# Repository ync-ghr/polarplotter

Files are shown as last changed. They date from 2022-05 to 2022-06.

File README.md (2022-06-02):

# Polar Plotter
Ein Projekt der Hochschule Pforzheim.

(https://youtu.be/9DOyNeQ_HOg)

- [Benötigte Komponenten](#benötigte-komponenten)<br>
  - [Zukaufteile](#zukaufteile)<br>
  - [3D-Druck Teile](#3d-druck-teile)<br>
- [Installation Polargraph Software](#installation-polargraph-software)<br>
- [Aufbau des Plotters](#aufbau-des-plotters)<br>
- [Einstellungen in der Software](#einstellungen-in-der-software)<br>

## Benötigte Komponenten

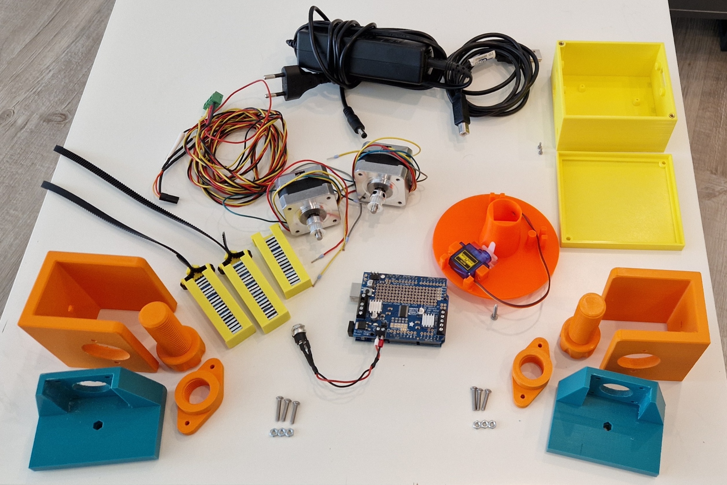
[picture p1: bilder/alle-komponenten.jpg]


### Zukaufteile

- Arduino Uno: http://store.arduino.cc/products/arduino-uno-rev3

- Adafruit Motor Shiled v2: https://www.adafruit.com/product/1438

- Servomotor: https://www.amazon.de/dp/B07CYZK379?ref_=cm_sw_r_cp_ud_dp_AW2FQ5ZJ4909N2ZZ1QXP
  - 5 V
  - 22,2 x 11,8 x 31 mm

- Schrittmotoren: https://www.adafruit.com/product/324#technical-details
  - 200 steps per revolution
  - 1.8 degrees
  - 12 V
  - 350 mA

- Zahnriemen und Zahnräder aus 3D-Drucker Bereich: https://www.amazon.de/dp/B07QH94G71?ref_=cm_sw_r_cp_ud_dp_NBP2886NY2H1YNJAXYJZ
  - GT2 2 mm
  - Rastermaß 6 mm
  - 5 m Länge

- Gewichte: https://www.amazon.de/dp/B08F2H4TB8?ref_=cm_sw_r_cp_ud_dp_EE6H5DKYBR2R5X1NX4WT 
  - 100 g + 2 x 60 g

- 12 V Netzteil

- Schrauben und Muttern:
  - 3x Rutex Gewindebuchse M3x5.7: https://www.ruthex.de/products/ruthex-gewindeeinsatz-m3-100-stuck-rx-m3x5-7-messing-gewindebuchsen
  - 8x M3x10 Schraube
  - 4x M3x15 Schraube
  - 3x M3x18 Schraube
  - 1x M3x30 Schraube
  - 6x M3 Mutter
  - 6x M2x5 Schraube (spitz)

### 3D-Druck Teile

STL-Dateien aus `/bauteile` auf dem 3D-Drucker herstellen. Die Komponenten und deren Funktionsweise werden [hier](stl\README.md) erläutert.

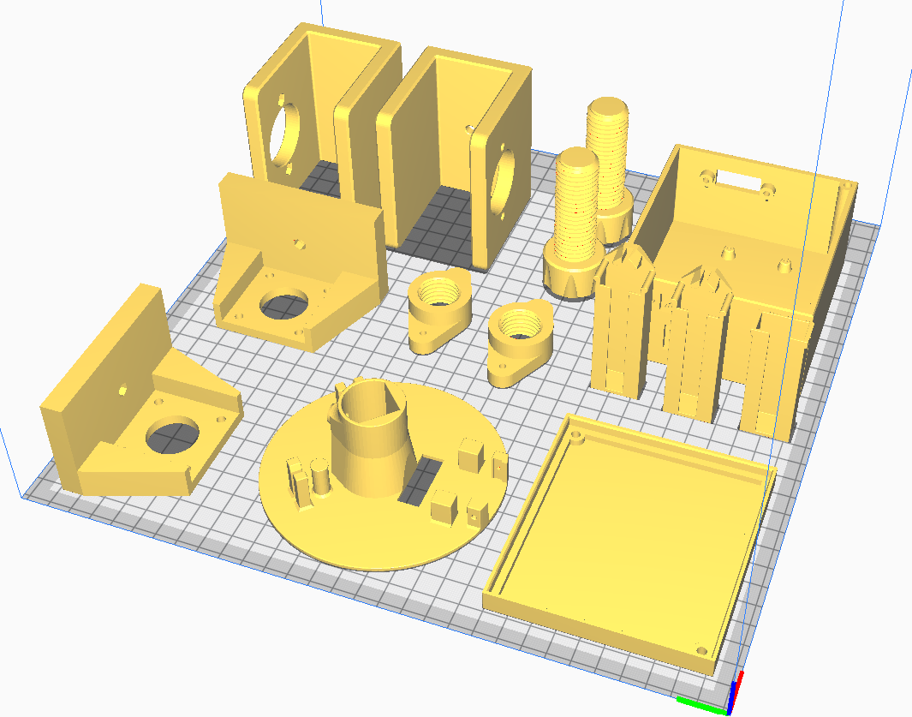
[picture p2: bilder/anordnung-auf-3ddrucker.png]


## Installation Polargraph Software

- Herunterladen und installieren von Arduino IDE v1.8.5: https://www.arduino.cc/en/software/OldSoftwareReleases#previous

- Herunterladen des Polargraphcontollers: https://github.com/euphy/polargraphcontroller/releases/tag/2017-11-01-20-30

- Dieses Verzeichnis (polargraph.2017-11-01.zip) entpacken und öffnen. Darin ist ein Ordner `\arduino-source\polargraph-server-a1` enthalten. Diesen in den Arduino Ordner verschieben (`C:\Users\"PCNAME"\Documents\Arduino`).

- Den Inhalt des Ordners `\arduino-source\libraries` in den Ordner `C:\Users\"PCNAME"\Documents\Arduino\libraries` verschieben. 
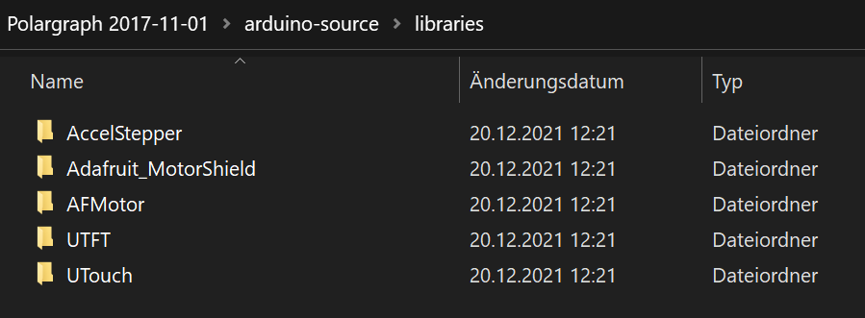
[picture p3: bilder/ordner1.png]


- Anschließend Arduino IDE starten und Arduino über USB mit dem PC verbinden.

- `File -> Sketchbook -> polargraph_server_a1` auswählen und im Tab polargraph_server_a1 unter 1. den Controller auf MC_UNO einstellen. Unter 3. die verwendeten Motortreiber auswählen.

  ```
  // 1. 
  //Uncomment the line for the kind of board you have.
  #ifndef MICROCONTROLLER
  #define MICROCONTROLLER MC_UNO
  //#define MICROCONTROLLER MC_MEGA
  #endif

  // 3. 
  //Specify what kind of motor driver you are using
  #define ADAFRUIT_MOTORSHIELD_V2
  #include <Wire.h>
  #include <Adafruit_MotorShield.h>
  #include "utility/Adafruit_PWMServoDriver.h"
  ```

- Auswahl des Boards: `Tools -> Board -> Arduino Uno`

- Setzen des angeschlossenen Ports: `Tools -> Port -> COMx`

- Auf den Pfeil klicken, um den Code auf den Arduino zu laden. Warten, bis Hochladen abgeschlossen ist.

- Herunterladen und installieren von Processing v2.2.1: https://processing.org/download?processing

- Processing starten und wieder schließen.

- Im bereits heruntergeladenen Verzeichnis (polargraph.2017-11-01) den Inhalt des Ordners `Polargraph.2017-11-01\processing-source\Processing libraries` nach `C:\Users\"PCNAME"\Documents\Processing\libraries` kopieren.
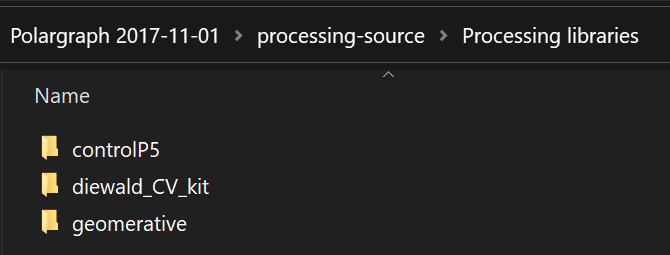
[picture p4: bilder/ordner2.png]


- Anschließend den gesamten Ordner `Polargraph 2017-11-01\processing-source\polargraphcontroller` in den Processing Sketchbook Ordner (`C:\Users\"PCNAME"\Documents\Processing`) kopieren.

- Processing erneut starten und `File -> Sketchbook -> polargraphcontroller` öffnen.

- Run drücken, um den Controller zu starten.

## Aufbau des Plotters

- Zusammenbau der beiden Motorhalterungen aus den 3D-Druckteilen, jeweils 3 Schrauben (2st M3x15, 1st M3x18) und 3 Muttern.

 
- Festschrauben der Motoren an der Halterung, Befestigung am Zeichenbrett und Anbringung der Zahnräder.
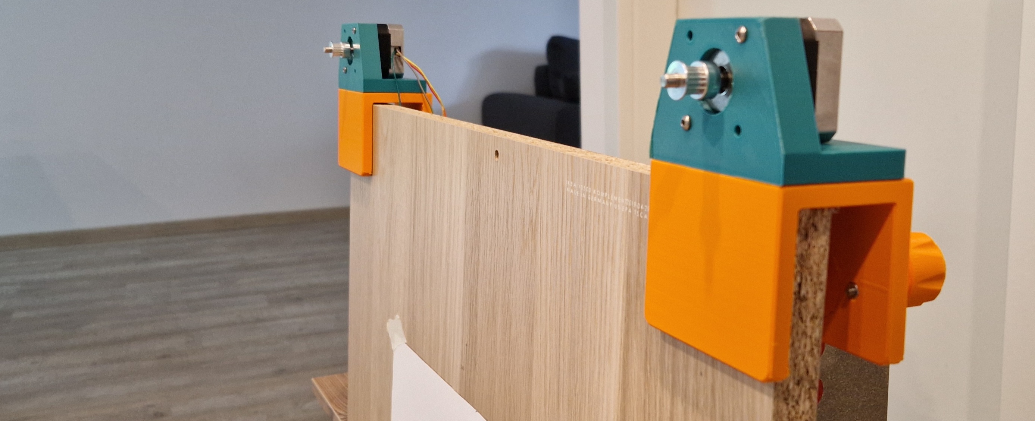
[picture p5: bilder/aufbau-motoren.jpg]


- Anbringen des Motorshields auf dem Arduino und löten der Pins. Anschließend vorbereiten der 12 V Stromversorgung.
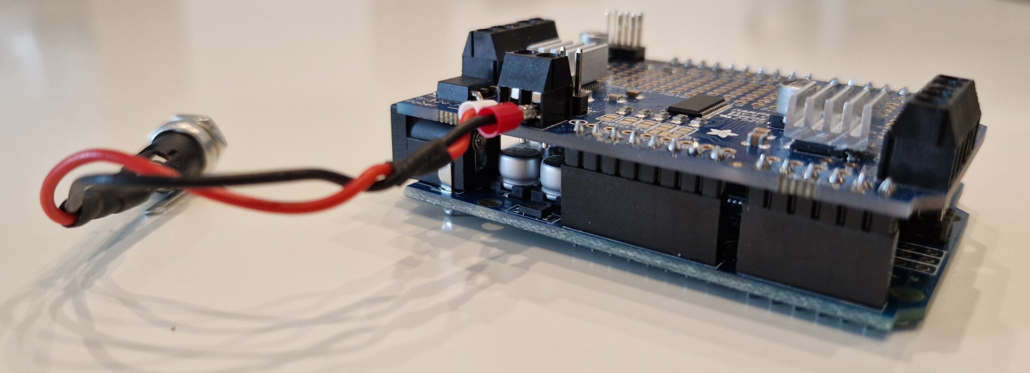
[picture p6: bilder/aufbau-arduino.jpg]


- Einlegen der Gewichte in die Halterungen und Befestigung des Gummiriemens durch Verkanten der Zähne. Riemen soll einmal gespiegelt angebracht werden (siehe Bild).
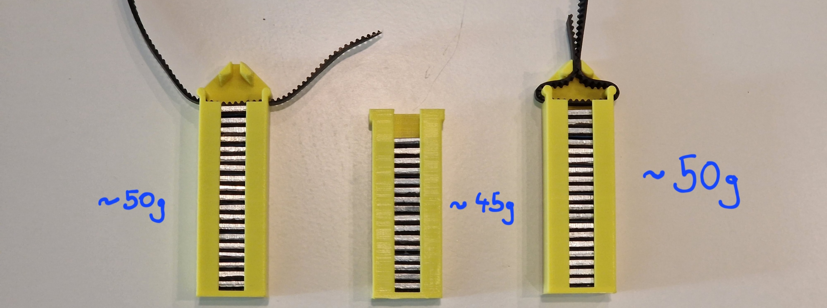
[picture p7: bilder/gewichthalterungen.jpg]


- Anbringen des Servomotors und der Gewichthalterung an der Gondel. Befestigung des Gummiriemens durch Verkanten. Verlängerungskabel für den Servomotor verbinden. Einschmelzen des Gewindes in die Bohrung.
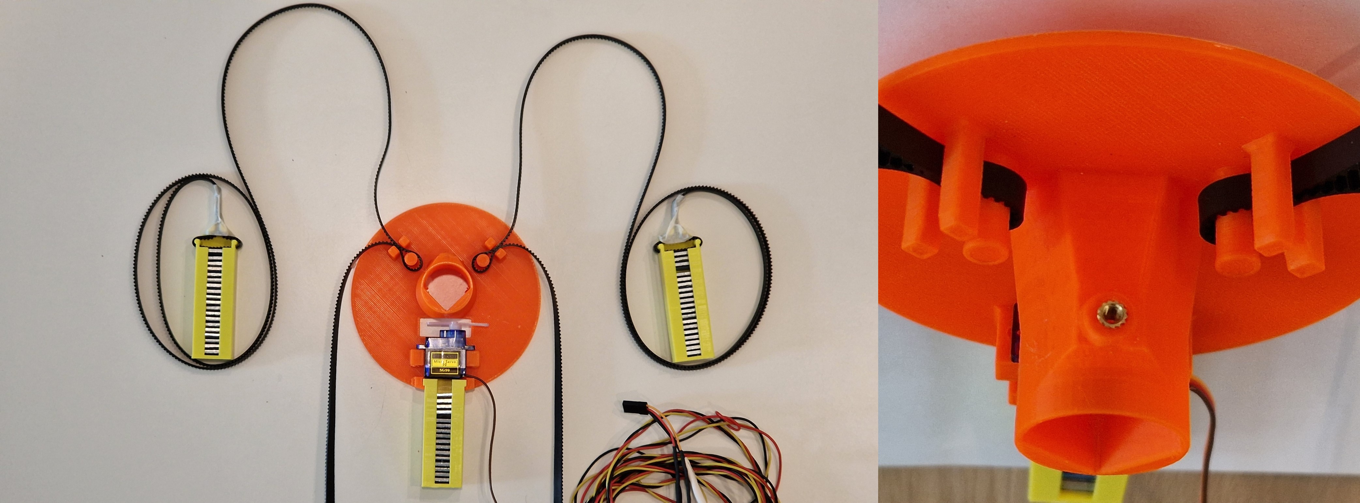
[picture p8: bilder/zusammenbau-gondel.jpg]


- Aufsetzen der Konstruktion über die Zahnräder und Kabel auf die Rückseite führen.
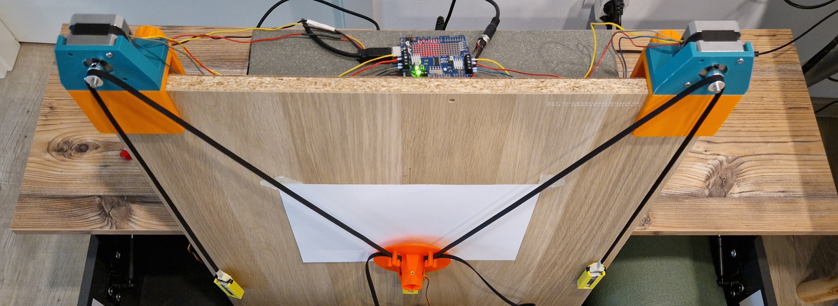
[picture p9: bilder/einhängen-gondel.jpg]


- Verkabelung der beiden Schrittmotoren an die Klemmen (Blau/Grün ein Coil, Gelb/Rot ein Coil) und aufstecken des Servosteckers an die Servo 2 Pins. Herstellen der 12 V Stromversorgung und der USB-Verbindung mit einem Windows-PC.


- Anbringung eines Zeichenblattes auf dem Zeichenbrett.

- Zum Schluss kann der Arduino in das gedruckte Gehäuse gesetzt und verschraubt werden.

## Einstellungen in der Software

### SETUP

Einstellungen für die Abmessungen des Zeichenbretts und des Zeichenblatts sowie weitere grundsätzliche Einstellungen. Im Tab SETUP.

| Feldname | Wert | Bedeutung |
|---|----:|---|
| MM PER REV | 64 | Drehung des Riemens pro Schritt |
| STEPS PER REV | 1090 | Schritte pro Umdrehung (alt. 400) |
| STEP MULTIPLIER | 6 | Skalierung der Schritte (alt. 16)|
| MASCHINE WIDTH | - | Breite des Zeichenbretts (Distanz zwischen Innenseite der Zahnräder) |
| MASCHINE HIGHT | - | Höhe des Zeichenbretts |
| PAGE WIDTH | - | Breite des Zeichenblatts |
| PAGE HIGHT | - | Höhe des Zeichenblatts |
| PAGE POS X | - | X-Position des Blatts |
| PAGE POS Y | - | Y-Position des Blatts |
| HOME POS X | - | X-Position des Homepunkts |
| HOME POS Y | - | Y-Position des Homepunkts |
| PEN UP POSTION | - | Winkel des Servos für angehobenen Stift |
| PEN DOWN POSITION | - | Winkel des Servos für abgesetzten Stift |
| MOTOR MAX SPEED | 1000 | Maximalgeschwindigkeit des Motors |
| MOTOR MAX ACCELERATION | 400 | Maximalbeschleunigung des Motors |

- Außerdem muss der `SERIAL PORT...` eingestellt werden. Ist die Verbindung erfolgreich, erscheint in grün `Polargraph READY! (Uno)`

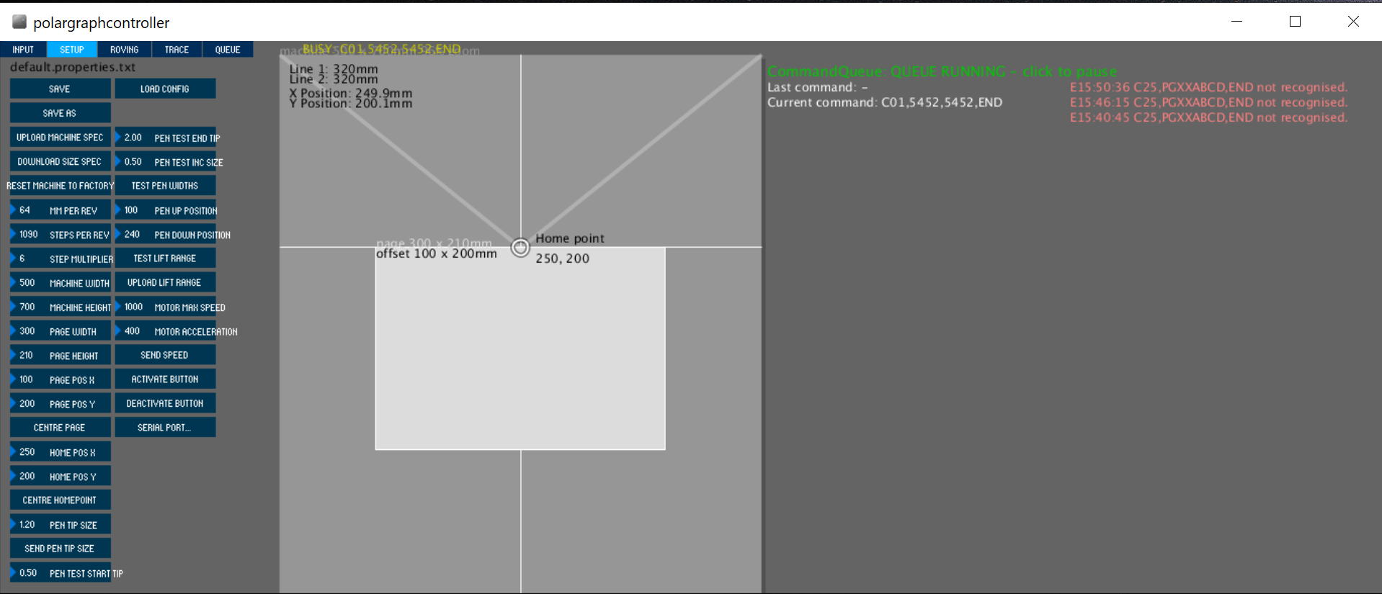
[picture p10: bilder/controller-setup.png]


### INPUT

Einstellungen, die das Zeichenobjekt betreffen. Über Tab INPUT.

- Zuerst muss die Gondel manuell so eingehängt werden, dass sich der Stift direkt über dem Homepunkt befindet. Anschließend kann über den Button `SET HOME` dieser Punkt abgespeichert werden.

- Durch Klicken auf den Button `LOAD IMAGE FILE` kann eine Bilddatei ausgewählt und auf dem Brett positioniert werden. Über `RESIZE IMAGE` und `MOVE IMAGE` kann die Größe und Position noch verändert werden.

- Es gibt die Möglichkeit ein Bild schattiert zu zeichnen, dafür `INPUT -> RENDER PIXELS`. Alternativ kann die Kontur eines Vektors oder Bilds gezeichnet werden, dafür `TRACE -> CAPUTER`, anschließend `DRAW CAPTURE` um den Code zu generieren.

- Durch klicken auf `QUEUE PAUSED` wird der gesendete Code ausgeführt.

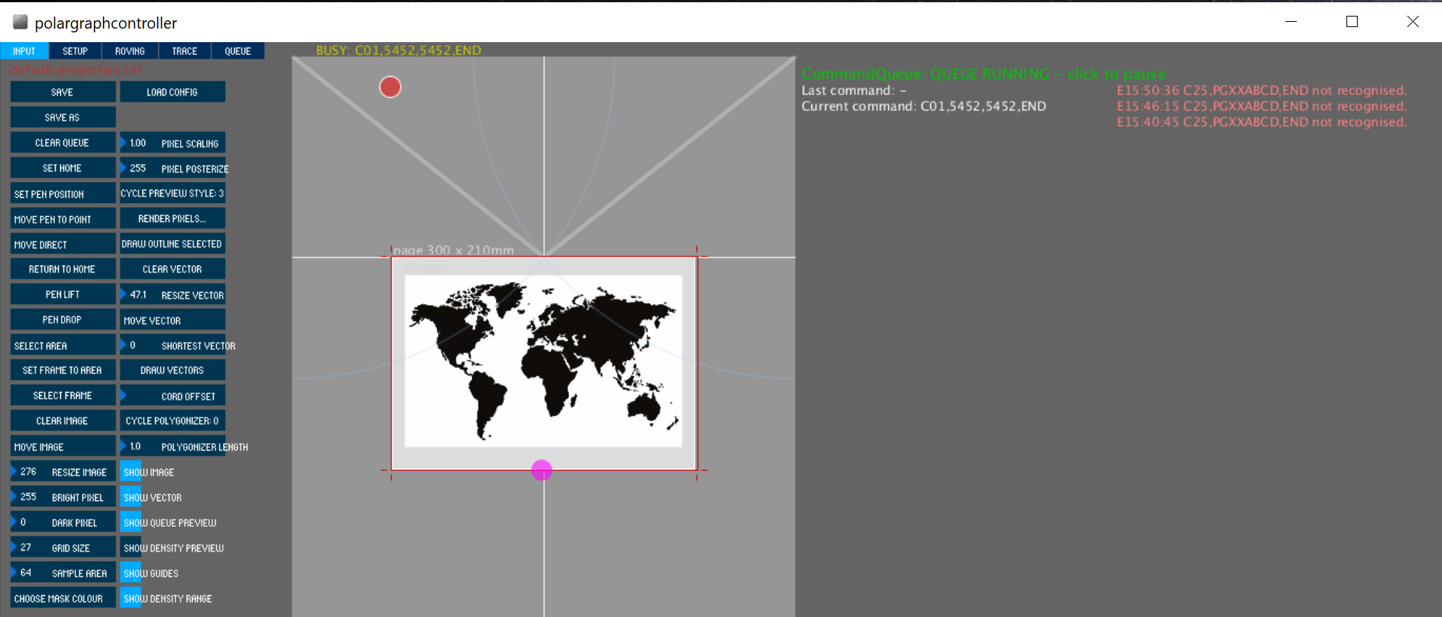
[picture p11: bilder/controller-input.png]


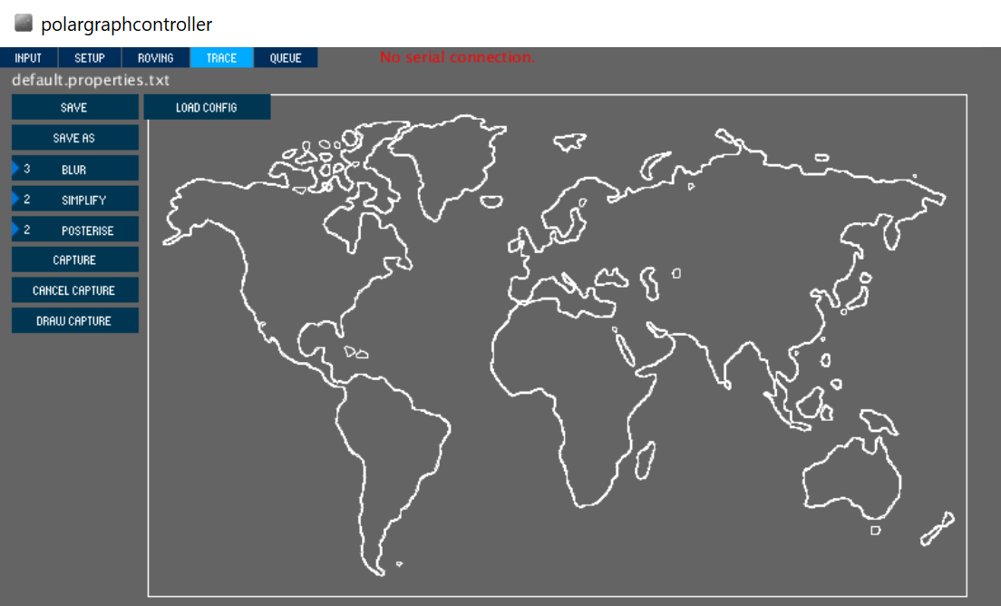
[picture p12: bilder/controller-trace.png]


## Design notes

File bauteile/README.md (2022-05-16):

# Beschreibung der Komponenten

[Deckel](#deckel)<br>
[Gehäuse](#gehäuse)<br>
[Gewichthalterung](#gewichthalterung)<br>
[Gondel](#gondel)<br>
[Gegen Gewichthalterung](#gegengewichthalterung)<br>
[Gewindeeinsatz](#gewindeeinsatz)<br>
[Klemme](#klemme)<br>
[Motorhalterung](#motorhalterung)<br>
[Schraube](#schraube)<br>

Über den Link in der jeweiligen Überschrift erfolgt eine Weiterleitung zum 3D-Modell.

## [Deckel](https://github.com/ync-ghr/polarplotter/blob/main/stl/1x_Deckel.stl)

- Der Deckel dient als Abdeckung und kann über die beiden Bohrungen mit dem Gehäuse verschraubt werden. 

## [Gehäuse](https://github.com/ync-ghr/polarplotter/blob/main/stl/1x_Geh%C3%A4use.stl)

- Das Gehäuse bietet die Möglichkeit, den Arduino darin fest zu verschrauben. Durch 3 M2x5 Schrauben kann durch die Bohrungen im Arduino eine Verbindung hergestellt werden.
- In die Bohrung kann die Klinkenbuchse des Netzteils gesetzt und durch Anziehen des Rings befestigt werden.
- Durch das Einsetzen von Ruthex Gewinden wird das Verschrauben des Deckels ermöglicht.
- Es gibt eine Aussparung für den USB-Port des Arduinos.
- Die Stecker der Motoren können optional mithilfe der Verbinder (siehe Bild) mit dem Gehäuse verschraubt werden. 


## [Gewichthalterung](https://github.com/ync-ghr/polarplotter/blob/main/stl/1x_Gewichthalterung.stl)

- Die Gewichthalterung bietet die Möglichkeit, Gewichte einzulegen und kann direkt mit der Gondel durch Formschluss verbunden werden. Darüber hinaus kann durch 2 M2 Schrauben abgesichert werden.

## [Gondel](https://github.com/ync-ghr/polarplotter/blob/main/stl/1x_Gondel.stl)

- Die Gondel hat einen Platz, um den Servomotor zu befestigen. Dieser kann außerdem verschraubt werden.
- Der Zylinder in der Mitte ist dazu gedacht, einen Stift hineinzustecken und durch eine Schraube zu fixieren.
- Die Riemen müssen um den kleinen Zylinder gelegt werden und werden durch Verkanten der Zähne und Fixieren in der Spalte befestigt (siehe Bild).

- Durch die Aussparung kann der Servo die Gondel von der Zeichenfläche wegdrücken und damit den Stift anheben.

## [Gegen Gewichthalterung](https://github.com/ync-ghr/polarplotter/blob/main/stl/2x_GegenGewichthalterung.stl)

- Die beiden Halterungen für Gegengewichte können ebenfalls wie die Gondel mit dem Riemen verbunden werden. Dieser wird durch die Aussparung geführt und dadurch verkantet (siehe Bild).


## [Gewindeeinsatz](https://github.com/ync-ghr/polarplotter/blob/main/stl/2x_Gewindeeinsatz.stl)

- Der Gewindeeinsatz hat ein M20 Gewinde und 2 Bohrungen. Damit kann das Gewinde separat von der Klemme hergestellt werden. Das bietet den Vorteil, es senkrecht stehend drucken zu können und bei einer Beschädigung kann dieses Bauteil leicht ersetzt werden.
- Es passt genau in die Bohrung der Klemme.

## [Klemme](https://github.com/ync-ghr/polarplotter/blob/main/stl/2x_Klemme.stl)

- Die Klemme wird über ein Zeichenbrett/Flipchart/Metaplanwand gesetzt und kann dort ganz leicht mit der ebenfalls gedruckten Schraube befestigt werden.
- Auf der Oberseite ist eine quadratische Aussparung, um dort das Gegenstück, welches sich auf der Unterseite der Motorhalterung befindet, einzusetzen. Dadurch wird ein Verdrehen der beiden Bauteile zueinander verhindert.

## [Motorhalterung](https://github.com/ync-ghr/polarplotter/blob/main/stl/2x_Motorhalterung.stl)

- In der Motorhalterung befindet sich eine Bohrung, durch welche die Welle des Schrittmotors passt.
- Zusätzlich- kann dieser durch 4 Bohrungen mit der Halterung verschraubt werden.
- Durch die Seitenwände wird die Positionierung vereinfacht.
- Auf der Unterseite befindet sich die schon angesprochene Erhöhung.

## [Schraube](https://github.com/ync-ghr/polarplotter/blob/main/stl/2x_Schraube.stl)

- Die Schraube passt genau in den Gewindeeinsatz und befestigt die Klemme und Motorhalterung auf einem Brett.
- Der Kopf ist so konzipiert, dass er ohne Werkzeug verschraubt werden kann.

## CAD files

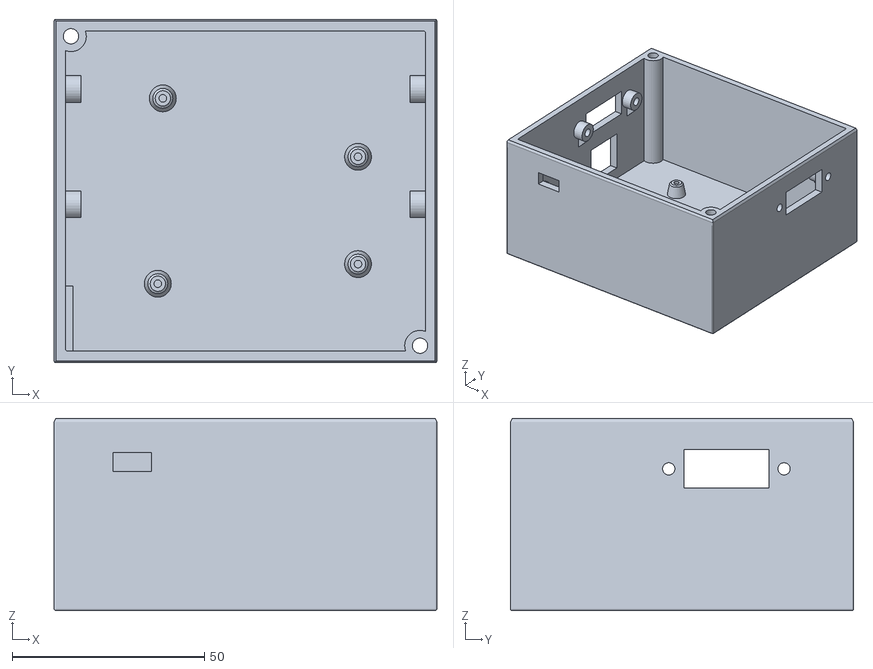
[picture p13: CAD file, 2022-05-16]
bauteile/1x_Gehäuse.stl
99.6 x 89.3 x 50.0

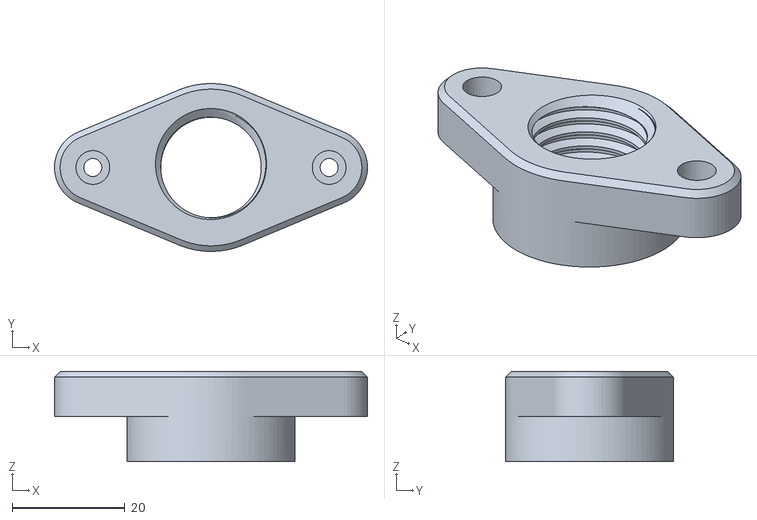
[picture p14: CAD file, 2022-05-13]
bauteile/2x_Gewindeeinsatz.stl
55.6 x 29.8 x 16.0

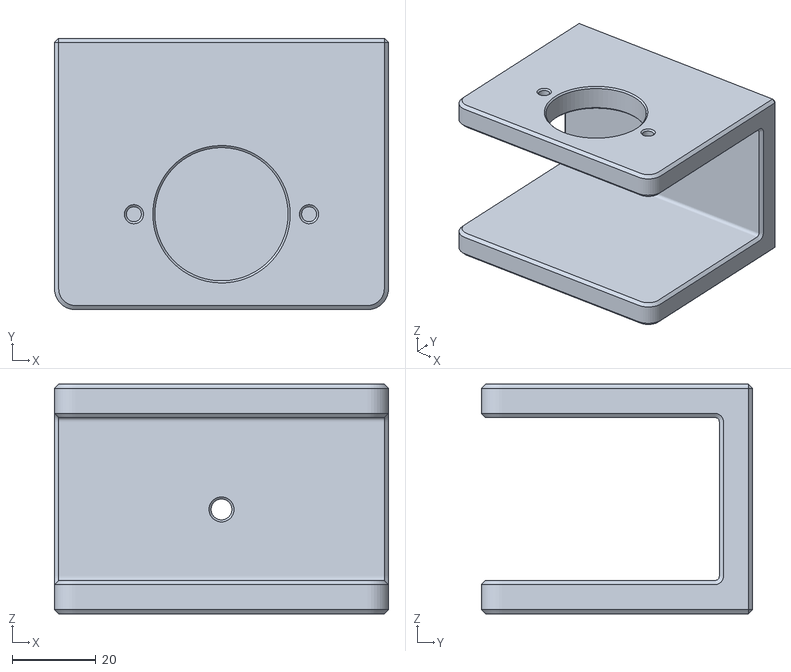
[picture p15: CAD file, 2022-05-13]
bauteile/2x_Klemme.stl
80.0 x 65.0 x 55.0

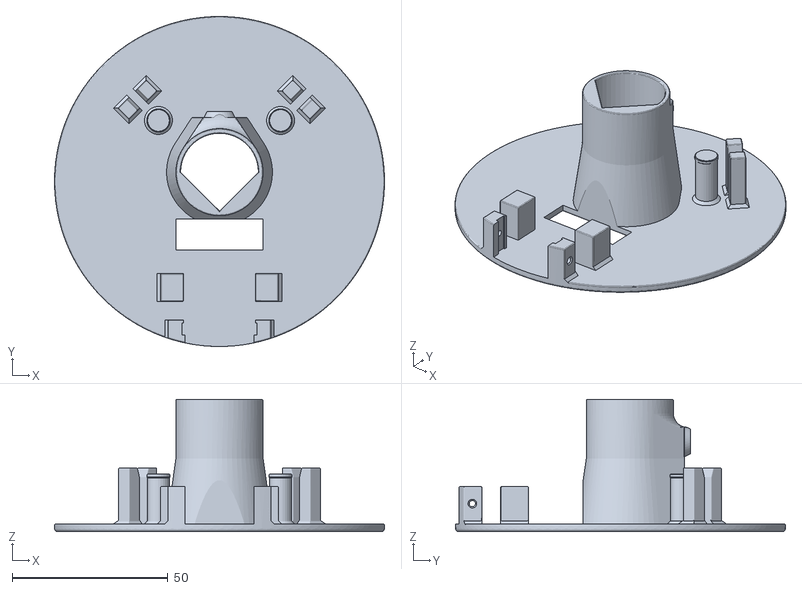
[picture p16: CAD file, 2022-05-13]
bauteile/1x_Gondel.stl
106.0 x 106.0 x 42.5

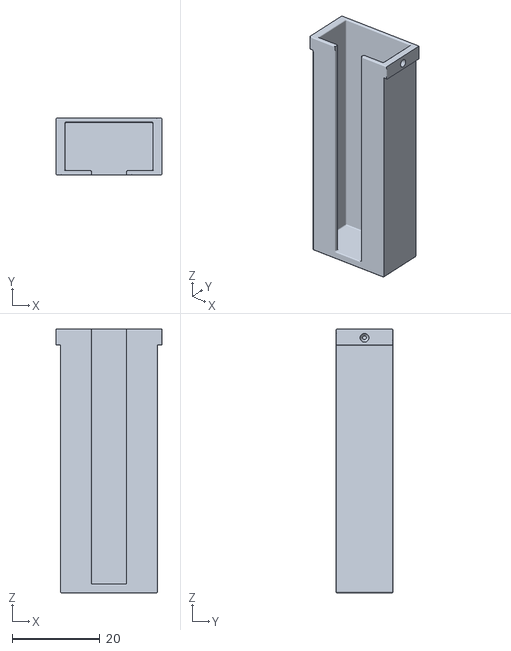
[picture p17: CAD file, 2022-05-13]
bauteile/1x_Gewichthalterung.stl
24.0 x 13.0 x 60.0

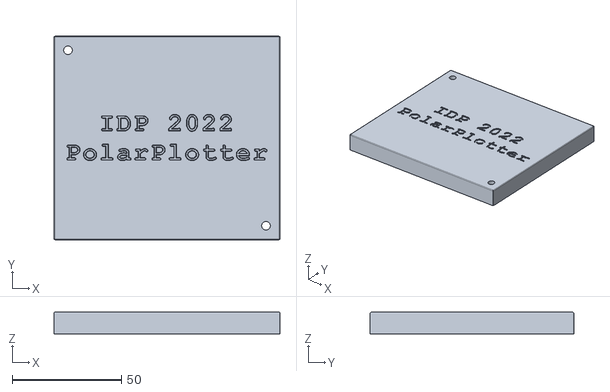
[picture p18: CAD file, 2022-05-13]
bauteile/1x_Deckel.stl
103.6 x 93.3 x 10.0

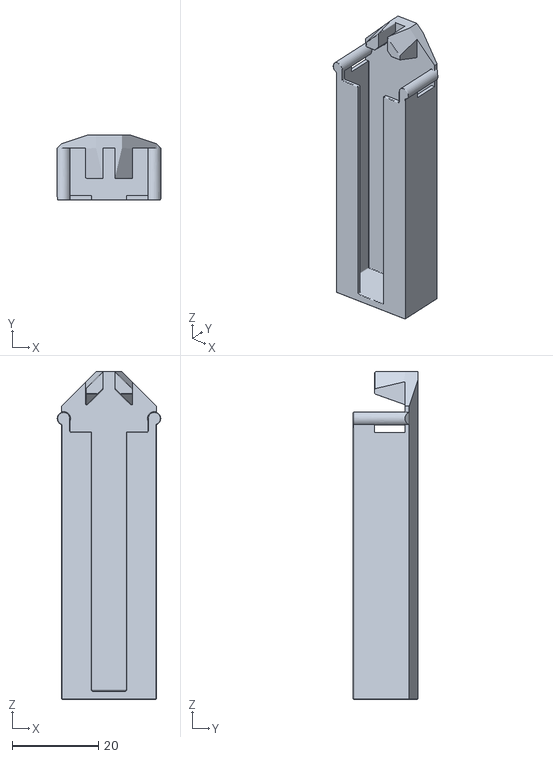
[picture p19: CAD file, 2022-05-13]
bauteile/2x_GegenGewichthalterung.stl
24.0 x 15.0 x 76.0

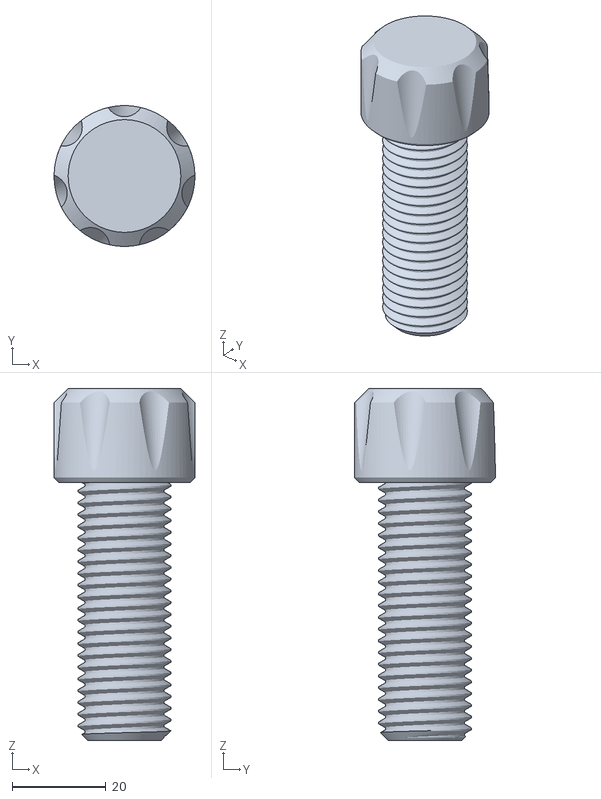
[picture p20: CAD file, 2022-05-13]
bauteile/2x_Schraube.stl
30.0 x 30.0 x 75.0

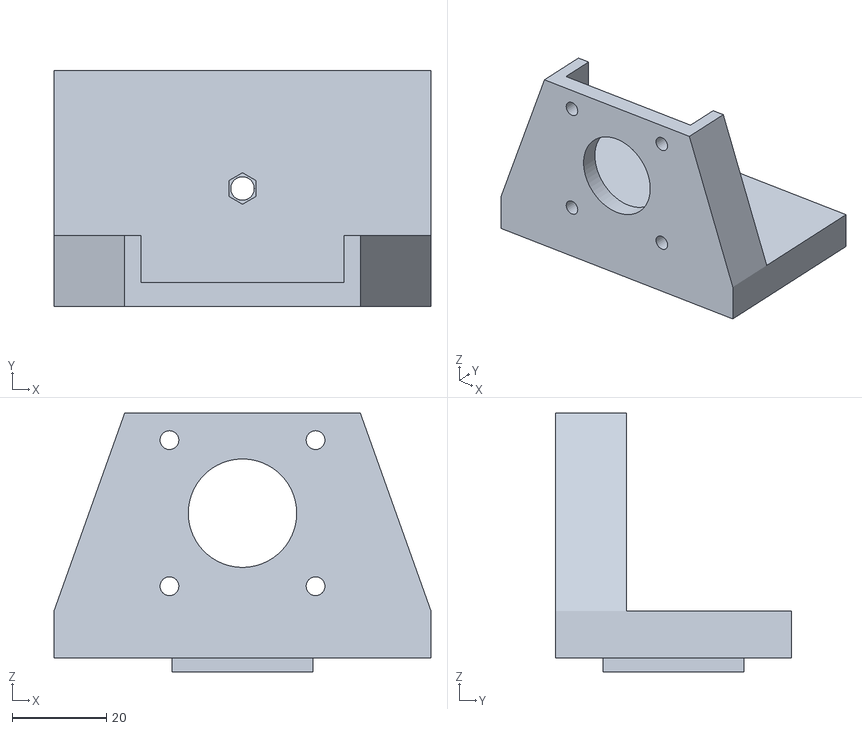
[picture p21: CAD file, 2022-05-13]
bauteile/2x_Motorhalterung.stl
80.0 x 50.0 x 55.0

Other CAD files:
bauteile/fusion360/GegenGewichthalterung.f3d
bauteile/fusion360/Gehäuse-Deckel.f3z
bauteile/fusion360/Gewichthalterung.f3d
bauteile/fusion360/Gondel.f3z
bauteile/fusion360/Klemme-Schraube-Gewindeeinsatz.f3d
bauteile/fusion360/Motorhalterung.f3z

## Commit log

2022-05-13 moved into folder
    [1x_Deckel.stl, 1x_Gehäuse.stl, 1x_Gewichthalterung.stl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]
2022-05-17 inital commit
    [1x_Deckel.stl, 1x_Gehäuse.stl, 1x_Gewichthalterung.stl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]
